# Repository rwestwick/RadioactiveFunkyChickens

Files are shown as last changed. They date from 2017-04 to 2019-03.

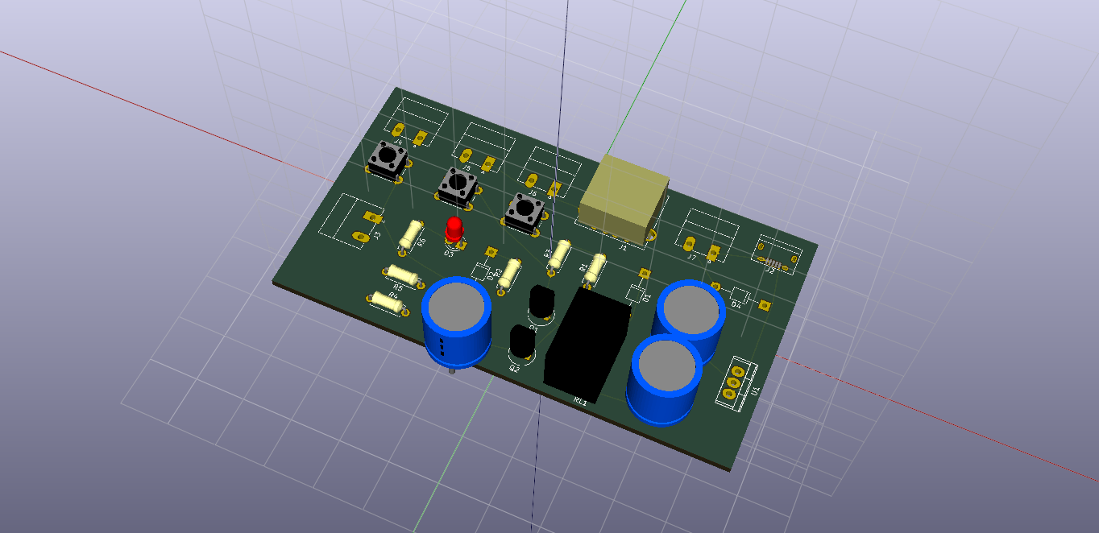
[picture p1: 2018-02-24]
Design/electronics/PiPowerSupplyCircuit/PowerSupplyAndSafeOff.png

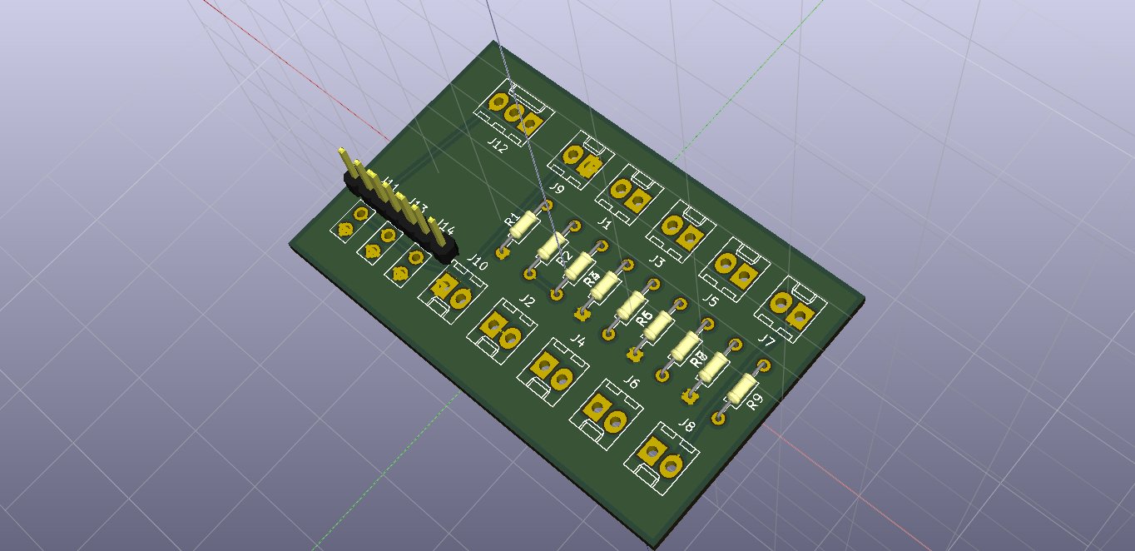
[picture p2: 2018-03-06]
Design/electronics/InterfaceBoard/InterfaceBoard.png

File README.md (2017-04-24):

# RadioactiveFunkyChickens

These are the Python files for the RadioactiveFunkyChickens team's PiWars robot.

## Files

### Challenge code

- LineFollowingAlgorithm.py: Code for the [line following challenge] (http://piwars.org/2017-competition/challenges/line-following/)
- MinimalMazeAlgorithm.py: Code for the [Minimal Maze challenge (http://piwars.org/2017-competition/challenges/minimal-maze/)
- straightLineSpeedTest2.py: Code for the [straight line speed test challenge] (http://piwars.org/2017-competition/challenges/straight-line-speed-test/)
- WiimoteControllerNunchukEye.py: Remote controller code to the non-autonomous PiWars challenges. Needs Wiimote Nunchuck and can control the servos for pan and tilt.

### Initio code

Several of the Python files are downloaded from the 4tronix web site to work with the Initio and Robohat hardware.

## See Also

- [RadioactiveFunkyChickens Blog] (https://radioactivefunkychickens.wordpress.com/)
- [PiWars] (http://piwars.org/)
- [Raspberry Pi] (http://www.raspberrypi.org/)
- [4tronix Initio Home Page] (http://4tronix.co.uk/blog/?p=169)

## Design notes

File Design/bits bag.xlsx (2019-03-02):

Hackaday perma proto black hat | £7.50 | https://thepihut.com/products/adafruit-perma-proto-hat-for-pi-mini-kit-with-eeprom
Raspberry Pi 3 Desktop Kit | £50.00 | https://thepihut.com/products/raspberry-pi-3-desktop-kit
Picon Zero - Intelligent Robotics Controller for Raspberry Pi | £16.00 | https://shop.pimoroni.com/products/picon-zero-intelligent-robotics-controller-for-raspberry-pi
RasPiO InsPiRing - Straight 8 + Driver | £10.00 | https://shop.rasp.io/collections/raspio-collection/products/raspio-inspiring-programmable-rgb-led-shapes-super-bright-and-colourful
PIR Motion Sensor Module | £2.00 | https://thepihut.com/products/pir-motion-sensor-module
Pi-DACZero (Pre Soldered) | £16.50 | http://iqaudio.co.uk/hats/38-pi-daczero.html
Raspberry Pi 3B+ with 16GB MicroSD | £40.00 | https://thepihut.com/collections/raspberry-pi-3b/products/raspberry-pi-3-model-b-plus
Weird Wiley bag x 2 | £0.00 | ??
Nostarch Book voucher (Code is good for one ebook up to $50) | £36.00 | www.nostarch.com | Code is good for one ebook up to $50
 | £178.00

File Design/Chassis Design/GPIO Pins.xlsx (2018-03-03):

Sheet: Current GPIO Pins - Robohat
 | Pin No.
 | 1 | 2
 | 3 | 4
 | 5 | 6
Not on Robohat | 7 | 8
 | 9 | 10
Not on Robohat | 11 | 12 | Sonar Left
Free Input on GPIO | 13 | 14
Sonar Left | 15 | 16 | Sonar Right
 | 17 | 18 | Servo
 | 19 | 20
 | 21 | 22 | Servo
 | 23 | 24
 | 25 | 26
 | 27 | 28
Not on Robohat | 29 | 30
Sonar Right | 31 | 32 | Right Motor
Right Motor | 33 | 34
Left Motor | 35 | 36 | Left Motor
Not on Robohat | 37 | 38 | Sonar Front
 | 39 | 40 | Not on Robohat

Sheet: GPIO Pins - L298N
 | Pin No.
 | 1 | 2
 | 3 | 4
 | 5 | 6
Left Motor - Rear | 7 | 8
 | 9 | 10
Left Motor - Rear | 11 | 12 | Sonar Left
Free | 13 | 14
Sonar Left | 15 | 16 | Sonar Right
 | 17 | 18 | Servo
 | 19 | 20
 | 21 | 22 | Servo
 | 23 | 24
 | 25 | 26
 | 27 | 28
Right Motor - Rear | 29 | 30
Sonar Right | 31 | 32 | Right Motor - Front
Right Motor - Front | 33 | 34
Left Motor - Front | 35 | 36 | Left Motor - Front
Right Motor - Rear | 37 | 38 | Sonar Front
 | 39 | 40 | Sonar Front
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

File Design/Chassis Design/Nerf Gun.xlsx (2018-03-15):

Theta | 30 | deg | One direction
Adjacent | 35 | mm
Opposite | 20.20725942 | mm
Travel for positive and negative angle
 | 40.41451884 | mm

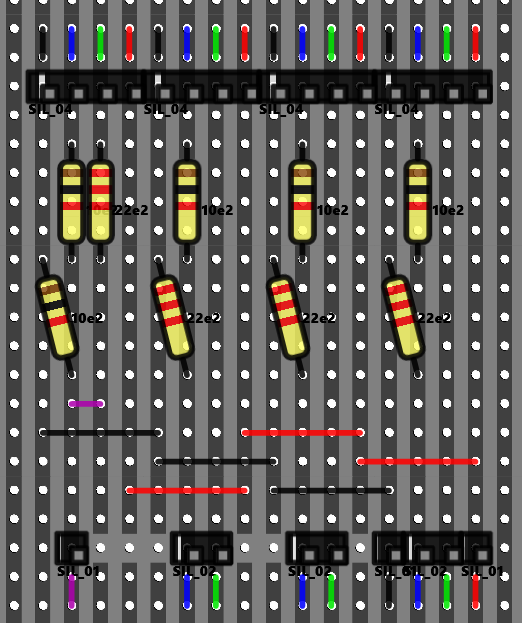
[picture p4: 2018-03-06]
Design/electronics/ultrasonic/ultrasonic.png

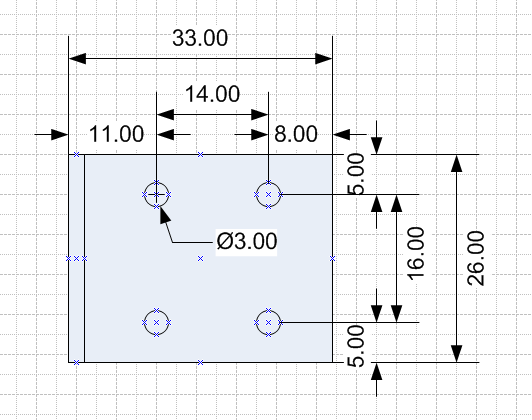
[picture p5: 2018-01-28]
Design/Chassis Design/6v_Motor_Bracket.png

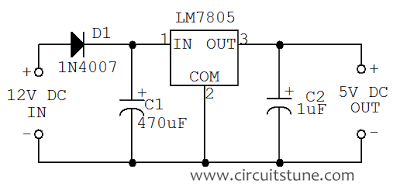
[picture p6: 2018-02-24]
Design/electronics/PiPowerSupplyCircuit/12-to-5-volt-dc-to-dc-converter-circuit-diagram.png

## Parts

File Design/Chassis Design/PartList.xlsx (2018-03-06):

Item | RS Code | Pack # | Per | Price (inc vat) | Total
Phoenix Contact COMBICON MPT Series 2.54mm Pitch Straight, PCB Terminal Block, Through Hole, 2 Way | 220-4260 | 5 | 5 | £0.49 | £2.47
Molex KK 254 6410, 2.54mm Pitch, 6 Way, 1 Row, Straight PCB Header, Through Hole | 483-8506 | 10 | 10 | £0.32 | £3.15
Bright Zinc Plated, Clear Passivated Steel Pan Head Machine Screws, M3 x 10mm | 560-596 | 100 | 1 | £2.81 | £2.81
Bright Zinc Plated, Clear Passivated Steel Pan Head Machine Screws, M3 x 12mm | 560-603 | 100 | 1 | £3.04 | £3.04
Molex KK 254 6471, 2.54mm Pitch, 6 Way, 1 Row Female Straight Connector Housing | 296-4984 | 5 | 5 | £0.54 | £2.70

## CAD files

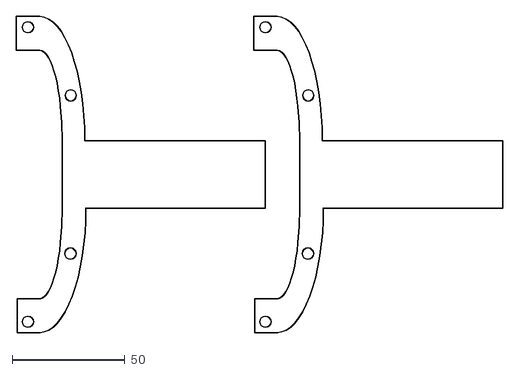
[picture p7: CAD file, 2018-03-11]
Design/Chassis Design/Slightly Deranged Golf - Layers.dxf
215.6 x 140.0

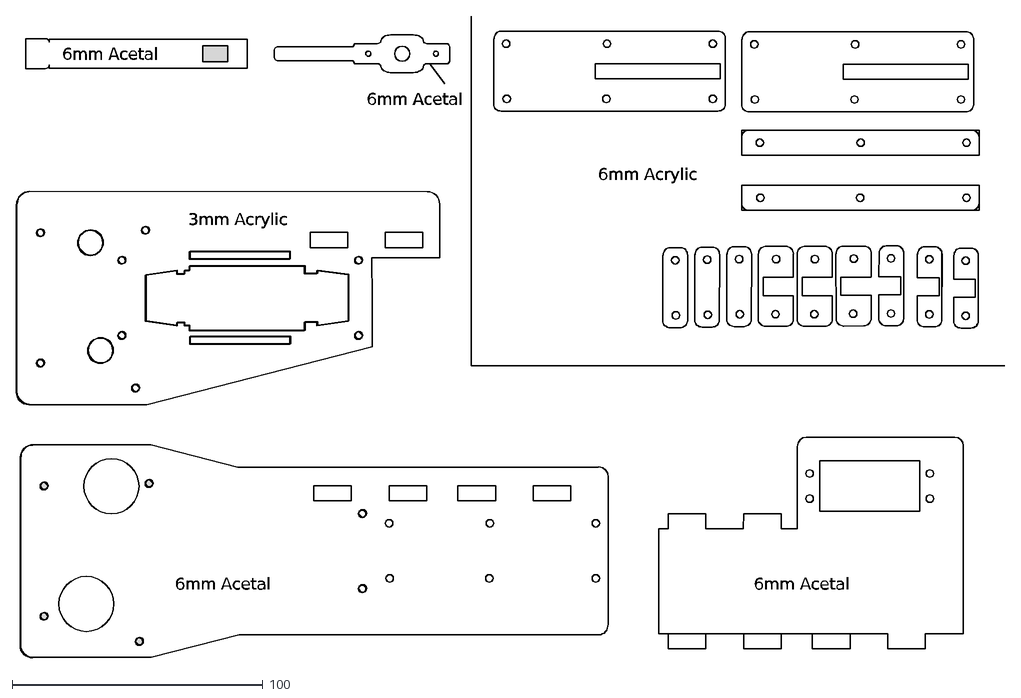
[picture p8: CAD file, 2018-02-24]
Design/Chassis Design/Nerf Holder.dxf
6mm Acetal
3mm Acrylic
6mm Acrylic

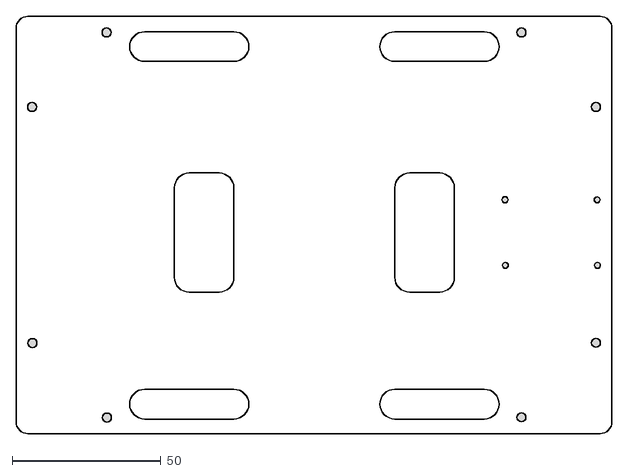
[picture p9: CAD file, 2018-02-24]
Design/Chassis Design/Pi Wars Chassis.dxf
200.0 x 140.0

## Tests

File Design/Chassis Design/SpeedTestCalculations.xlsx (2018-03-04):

Motor RPM | 270 | rpm
Wheel Dia | 65 | mm
Track Length | 7300 | mm
Rotation Lenth | 204.2 | mm
Num Rotations | 35.7 | #
Num Rotation per S | 4.5 | #
Est Time Taken | 7.94 | Seconds

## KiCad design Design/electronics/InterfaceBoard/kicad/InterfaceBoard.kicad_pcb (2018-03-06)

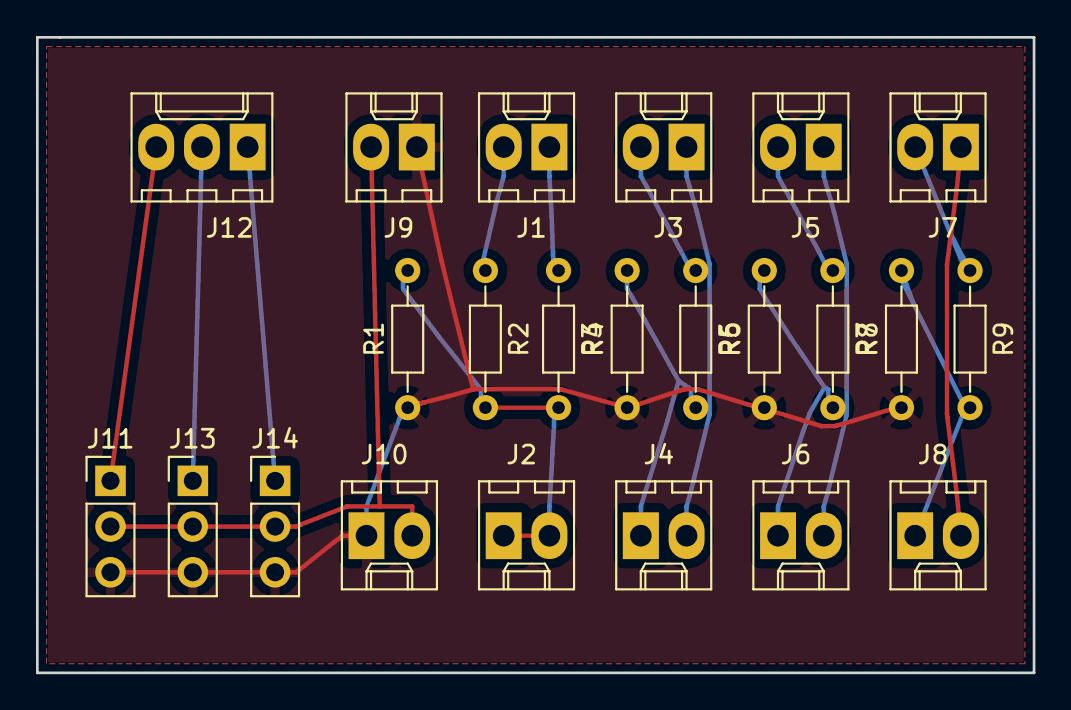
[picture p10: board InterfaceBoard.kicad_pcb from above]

Board: 2 copper layers, 55.4 x 35.3 mm, 23 parts (0 on the bottom side), 17 nets.

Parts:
J1, J2: PROX1; Molex_KK-6410-02_02x2.54mm_Straight
J3, J4: PROX2; Molex_KK-6410-02_02x2.54mm_Straight
J5, J6: PROX3; Molex_KK-6410-02_02x2.54mm_Straight
J7, J8: PROX4; Molex_KK-6410-02_02x2.54mm_Straight
J9: PWR IN; Molex_KK-6410-02_02x2.54mm_Straight
J10: PWR OUT; Molex_KK-6410-02_02x2.54mm_Straight
J11: HORZ; Pin_Header_Straight_1x03_Pitch2.54mm
J12: SERVO_IN; Molex_KK-6410-03_03x2.54mm_Straight
J13: VERT; Pin_Header_Straight_1x03_Pitch2.54mm
J14: FIRE; Pin_Header_Straight_1x03_Pitch2.54mm
R1, R2, R5, R7, R9: 1k; R_Axial_DIN0204_L3.6mm_D1.6mm_P7.62mm_Horizontal
R3, R4, R6, R8: 2k2; R_Axial_DIN0204_L3.6mm_D1.6mm_P7.62mm_Horizontal

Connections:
+5V: J9.2, J10.2, J11.2, J13.2, J14.2
GND: J9.1, J10.1, J11.3, J13.3, J14.3, R1.1, R4.1, R6.1, R8.1
unnamed: J1.1, R3.1
unnamed: J1.2, R2.1
unnamed: J2.1, J2.2, R1.2, R2.2, R3.2
unnamed: J3.1, J4.2
unnamed: J3.2, R5.1
unnamed: J4.1, R4.2, R5.2
unnamed: J5.1, J6.2
unnamed: J5.2, R7.1
unnamed: J6.1, R6.2, R7.2
unnamed: J7.1, J8.2
unnamed: J7.2, R9.1
unnamed: J8.1, R8.2, R9.2
unnamed: J11.1, J12.3
unnamed: J12.1, J14.1
unnamed: J12.2, J13.1

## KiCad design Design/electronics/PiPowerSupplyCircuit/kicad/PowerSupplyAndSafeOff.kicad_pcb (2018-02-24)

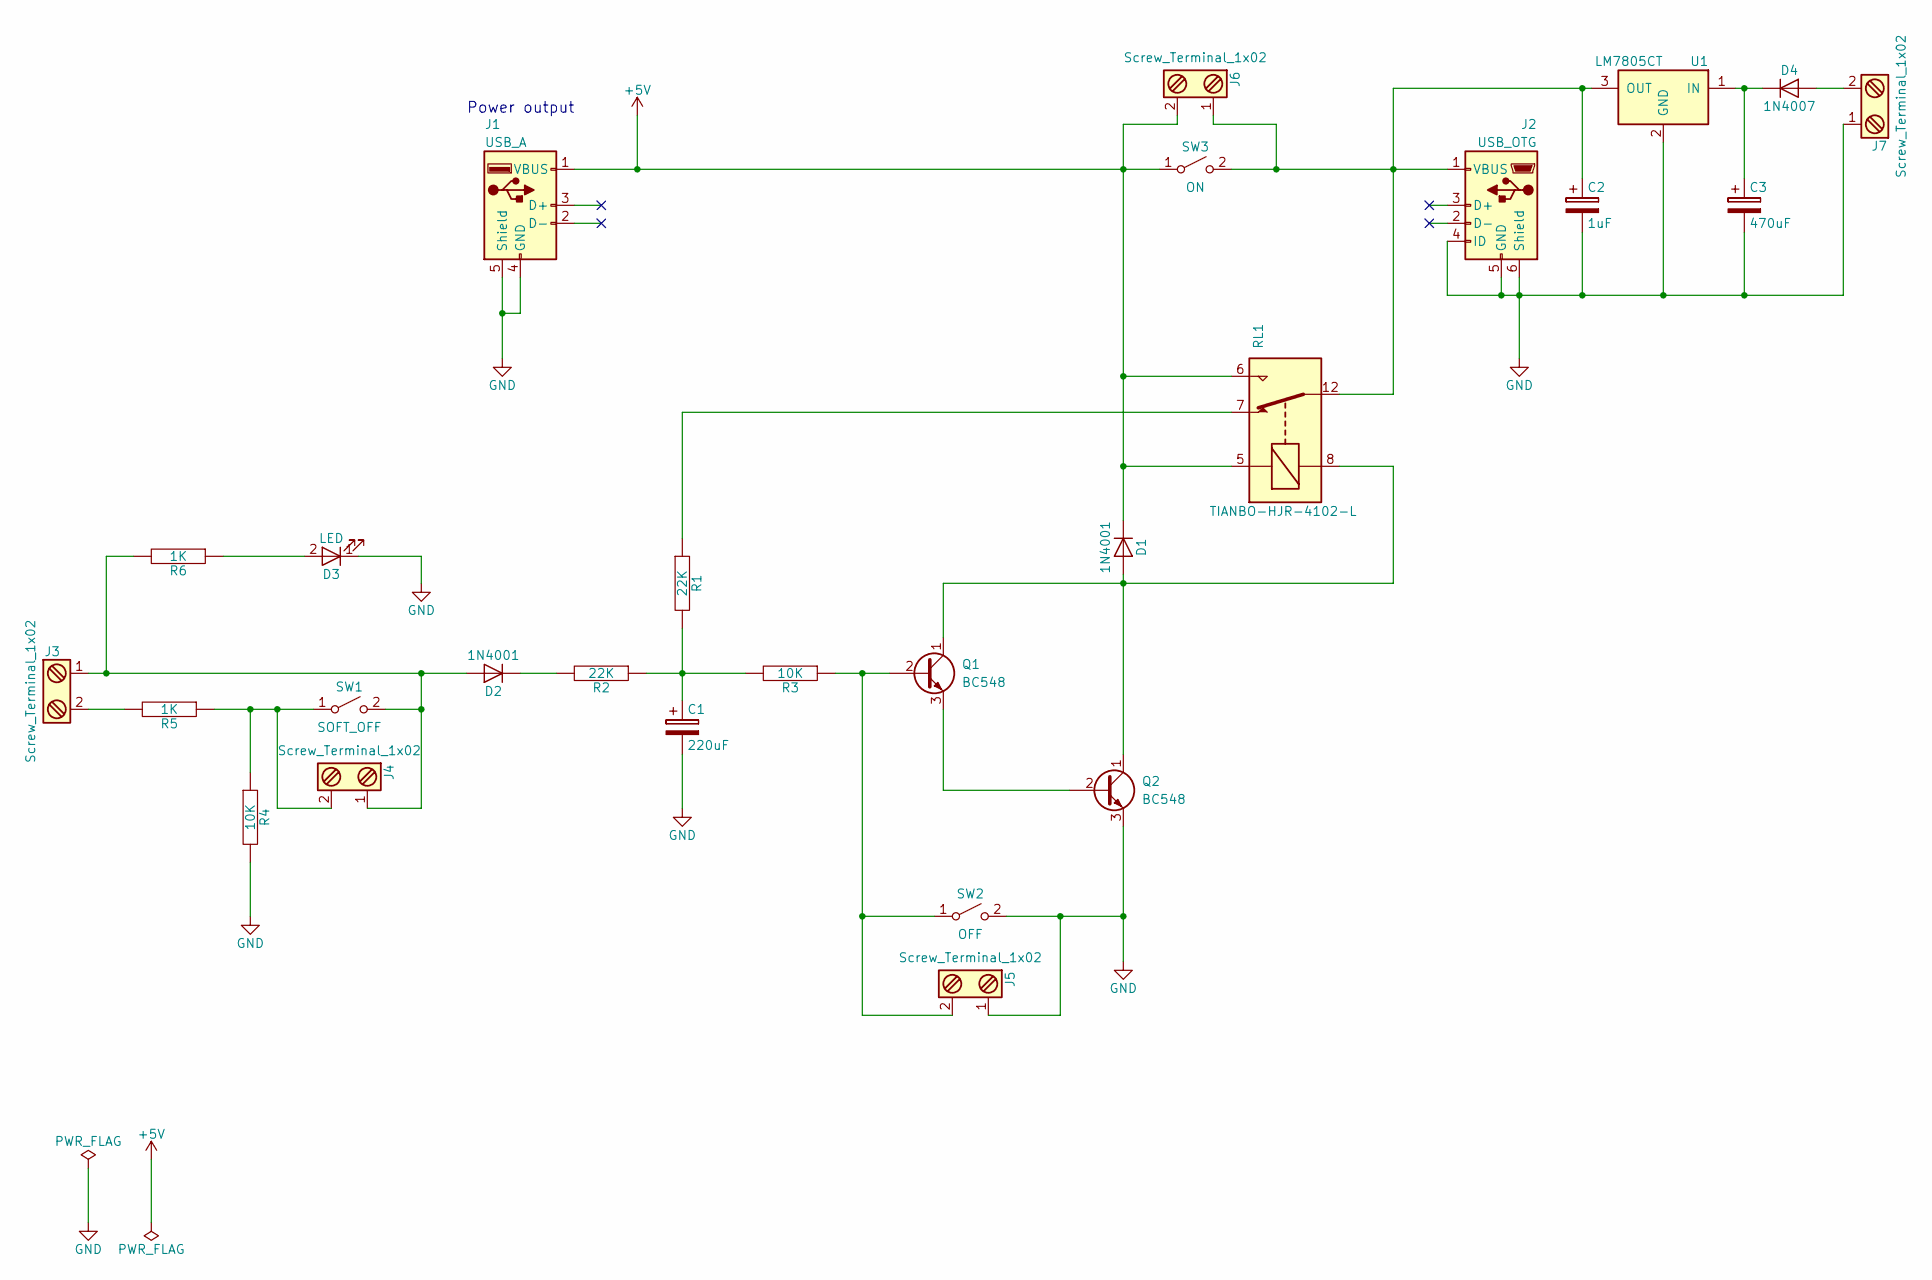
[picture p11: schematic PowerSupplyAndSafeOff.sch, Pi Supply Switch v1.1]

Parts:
C1: 220uF; CP_Radial_D5.0mm_P2.50mm
C2: 1uF; CP_Radial_D5.0mm_P2.50mm
C3: 470uF; CP_Radial_D5.0mm_P2.50mm
D1, D2: 1N4001; D_T-1_P10.16mm_Horizontal
D3: LED; LED_D3.0mm
D4: 1N4007; D_T-1_P10.16mm_Horizontal
J1: USB_A
J2: USB_OTG; USB_Micro-B
J3, J4, J5, J6, J7: Screw_Terminal_1x02; PhoenixContact_MC-G_02x5.08mm_Angled
Q1, Q2: BC548; TO-92_Inline_Narrow_Oval
R1, R2: 22K; R_Axial_DIN0207_L6.3mm_D2.5mm_P7.62mm_Horizontal
R3, R4: 10K; R_Axial_DIN0207_L6.3mm_D2.5mm_P7.62mm_Horizontal
R5, R6: 1K; R_Axial_DIN0207_L6.3mm_D2.5mm_P7.62mm_Horizontal
RL1: TIANBO-HJR-4102-L; Relay_SPDT_HJR-4102
SW1: SOFT_OFF; SW_PUSH_6mm_h4.3mm
SW2: OFF; SW_PUSH_6mm_h4.3mm
SW3: ON; SW_PUSH_6mm_h4.3mm
U1: LM7805CT; TO-220

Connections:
+5V: D1.1 (K), J1.1 (VBUS), J6.2, RL1.5, RL1.6, SW3.1 (A)
GND: C1.2, C2.2, C3.2, D3.1 (K), J1.4 (GND), J1.5 (Shield), J2.4 (ID), J2.5 (GND), J2.6 (Shield), J5.1, J7.1, Q2.3 (E), R4.2, SW2.2 (B), U1.2 (GND)
unnamed: C1.1, R1.2, R2.1, R3.2
unnamed: C2.1, J2.1 (VBUS), J6.1, RL1.12, SW3.2 (B), U1.3 (OUT)
unnamed: C3.1, D4.1 (K), U1.1 (IN)
unnamed: D1.2 (A), Q1.1 (C), Q2.1 (C), RL1.8
unnamed: D2.1 (K), R2.2
unnamed: D2.2 (A), J3.1, J4.1, R6.2, SW1.2 (B)
unnamed: D3.2 (A), R6.1
unnamed: D4.2 (A), J7.2
unnamed: J3.2, R5.2
unnamed: J4.2, R4.1, R5.1, SW1.1 (A)
unnamed: J5.2, Q1.2 (B), R3.1, SW2.1 (A)
unnamed: Q1.3 (E), Q2.2 (B)
unnamed: R1.1, RL1.7

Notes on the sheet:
Power output

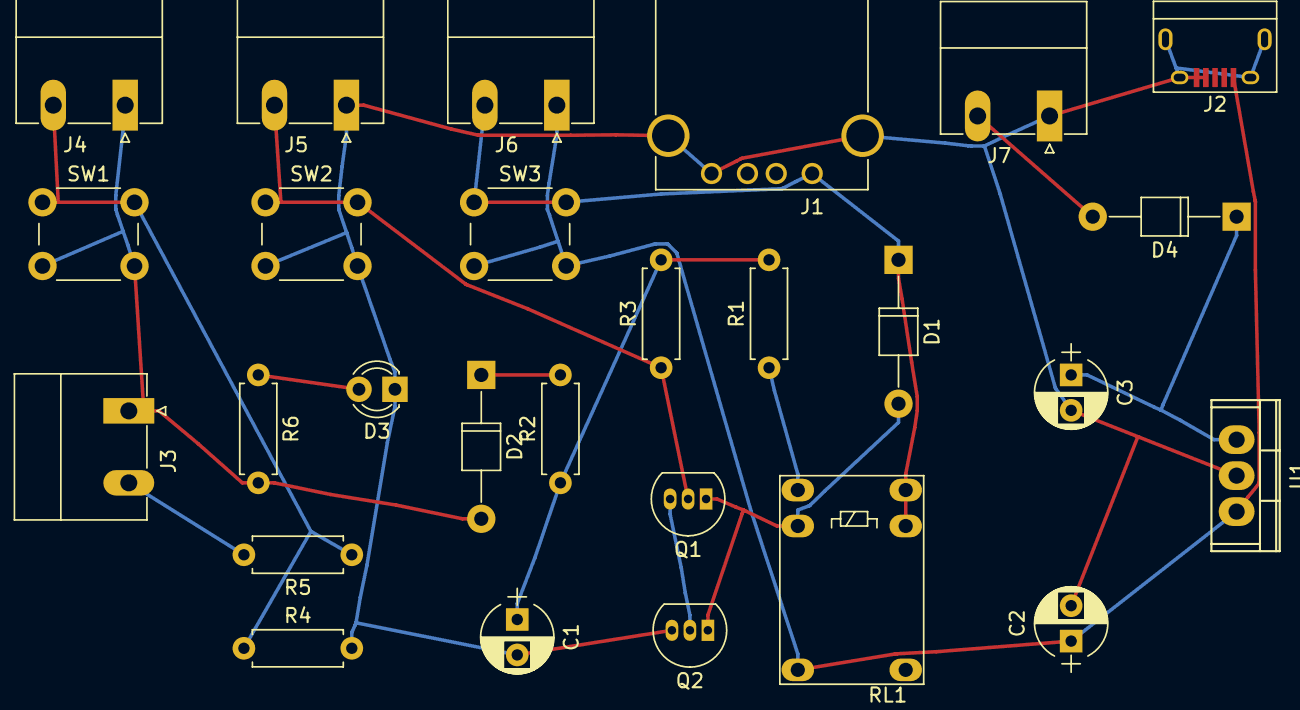
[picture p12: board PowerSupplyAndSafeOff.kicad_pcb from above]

Board: 2 copper layers, 27 parts (0 on the bottom side), 15 nets.

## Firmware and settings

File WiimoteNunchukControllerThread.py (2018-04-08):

#!/usr/bin/python
"""
Class defines how to interact with a Wiimote and Nunchuk
Controller via a thread

Need to install correct python modules, see
https://help.ubuntu.com/community/CWiiD
"""

import time
import logging
import threading
import math
import cwiid
import ServoController
import DualMotorController
import GPIOLayout
import SpeedSettings

MODULE_LOGGER = logging.getLogger("__main__.WiimoteNunchukControllerThread")


class WiimoteNunchukControllerThread(threading.Thread):
    """
    Defines the generic wiimote and nunchuk control mechanism
    """
    # Set constants
    STICK_DELAY = 0.1  # seconds
    BUTTON_DELAY = 0.25  # seconds
    PAN_STEP = 10
    TILT_STEP = 10
    NUNCHUK_MAX = 220.0
    NUNCHUK_MID = 126.0
    NUNCHUK_MIN = 32.0
    NUNCHUK_BUFFER = 25.0

    def __init__(self,
                 callback_b,
                 callback_c,
                 callback_z,
                 servo_controller=None):
        """
        Initialise the parameters required for WiimoteNunchukControllerThread
        """
        MODULE_LOGGER.info("Setting up WiimoteNunchukControllerThread Module")

        self._mutex = threading.Lock()
        self.t_val = 0  # 0 degrees is centre
        self.p_val = 0  # 0 degrees is centre

        self._exit_now = False
        self._servo_supplied = False
        self._button_b_callback = callback_b
        self._button_c_callback = callback_c
        self._button_z_callback = callback_z
        self.speed = SpeedSettings.SPEED_FASTEST  # Initial forward speed
        self.servo_controller = None

        # Initialise motors
        self.robotmove = DualMotorController.DualMotorController(
            GPIOLayout.MOTOR_LEFT_FRONT_FORWARD_GPIO,
            GPIOLayout.MOTOR_LEFT_FRONT_BACKWARD_GPIO,
            GPIOLayout.MOTOR_RIGHT_FRONT_FORWARD_GPIO,
            GPIOLayout.MOTOR_RIGHT_FRONT_BACKWARD_GPIO,
            GPIOLayout.MOTOR_LEFT_REAR_FORWARD_GPIO,
            GPIOLayout.MOTOR_LEFT_REAR_BACKWARD_GPIO,
            GPIOLayout.MOTOR_RIGHT_REAR_FORWARD_GPIO,
            GPIOLayout.MOTOR_RIGHT_REAR_BACKWARD_GPIO)

        # Initialise ServoController
        if servo_controller is not None:
            MODULE_LOGGER.debug("Using supplied servo controller")
            self.servo_controller = servo_controller
            self._servo_supplied = True
        else:
            MODULE_LOGGER.debug("Creating servo controller")
            self.servo_controller = ServoController.ServoController()
            self._servo_supplied = False

        self.servo_controller.start_servos()

        # Wiimote Controller
        self.wm = None

        threading.Thread.__init__(self)

    def __del__(self):
        """
        Destructor
        """
        if not self._exit_now:
            self.exit_now()

        if not self._servo_supplied and self.servo_controller is not None:
            self.servo_controller.stop_servos()

        self.robotmove.cleanup()
        MODULE_LOGGER.info("Wiimote Controller Finished")

    def __wiimote_connection(self):
        """
        Performs the loop within the thread
        """
        MODULE_LOGGER.info("Press 1+2 on your Wiimote now ...")

        i = 1
        while not self.wm and not self._exit_now:
            try:
                self.wm = cwiid.Wiimote()
            except RuntimeError:
                if (i > 5):
                    MODULE_LOGGER.error("Cannot create Wiimote connection.")
                    self.exit_now()
                MODULE_LOGGER.warning(
                    "Error opening wiimote connection, attempt " + str(i))
                i += 1

        if not self._exit_now:
            MODULE_LOGGER.info("Wiimote connected.")

            # Set wiimote to report button presses
            self.wm.rpt_mode = cwiid.RPT_BTN | cwiid.RPT_ACC | cwiid.RPT_EXT

            # Turn on led to show connected
            self.wm.led = 1

            # Add a delay to allow the wiimote to come up correctly
            time.sleep(1)

    def exit_now(self):
        """
        Request the thread to exit
        """
        MODULE_LOGGER.info("Request to exit")
        self._exit_now = True

    def run(self):
        """
        Performs the loop within the thread
        """
        self.__wiimote_connection()

        MODULE_LOGGER.debug("Starting loop thread")
        while not self._exit_now:
            if 'nunchuk' in self.wm.state:

                buttons = self.wm.state['buttons']
                nunchuck_buttons = self.wm.state['nunchuk']['buttons']

                # X axis: Left Max = 25, Middle = 124, Right Max = 225
                NunchukStickX = (self.wm.state['nunchuk']['stick'][cwiid.X])
                # Y axis: Down Max = 30, Middle = 132, Up Max = 225
                NunchukStickY = (self.wm.state['nunchuk']['stick'][cwiid.Y])

                # Go forward if joystick pushed forward beyond buffer in central
                # channel
                if (NunchukStickY > (self.NUNCHUK_MID + self.NUNCHUK_BUFFER)
                        and NunchukStickX <
                    (self.NUNCHUK_MID + self.NUNCHUK_BUFFER)
                        and NunchukStickX >
                        (self.NUNCHUK_MID - self.NUNCHUK_BUFFER)):

                    self.speed = int(SpeedSettings.SPEED_FASTEST *
                                     (NunchukStickY - self.NUNCHUK_MID) /
                                     (self.NUNCHUK_MAX - self.NUNCHUK_MID))
                    if self.speed > SpeedSettings.SPEED_FASTEST:
                        self.speed = SpeedSettings.SPEED_FASTEST

                    MODULE_LOGGER.debug("Forward at speed " + str(self.speed))
                    self.robotmove.forward(self.speed)
                    time.sleep(self.STICK_DELAY)

                # Go backwards if joystick pulled back beyond buffer in central
                # channel
                elif (NunchukStickY < (self.NUNCHUK_MID - self.NUNCHUK_BUFFER)
                      and NunchukStickX <
                      (self.NUNCHUK_MID + self.NUNCHUK_BUFFER)
                      and NunchukStickX >
                      (self.NUNCHUK_MID - self.NUNCHUK_BUFFER)):

                    self.speed = int(SpeedSettings.SPEED_FASTEST *
                                     (self.NUNCHUK_MID - NunchukStickY) /
                                     (self.NUNCHUK_MID - self.NUNCHUK_MIN))
                    if self.speed > SpeedSettings.SPEED_FASTEST:
                        self.speed = SpeedSettings.SPEED_FASTEST

                    MODULE_LOGGER.debug("Reverse at speed " + str(self.speed))
                    self.robotmove.reverse(self.speed)
                    time.sleep(self.STICK_DELAY)

                # Spin right right joystick pushed right beyond buffer in central
                # channel
                elif (NunchukStickX > (self.NUNCHUK_MID + self.NUNCHUK_BUFFER)
                      and NunchukStickY <
                      (self.NUNCHUK_MID + self.NUNCHUK_BUFFER)
                      and NunchukStickY >
                      (self.NUNCHUK_MID - self.NUNCHUK_BUFFER)):

                    self.speed = int(SpeedSettings.SPEED_FASTEST *
                                     (NunchukStickX - self.NUNCHUK_MID) /
                                     (self.NUNCHUK_MAX - self.NUNCHUK_MID))
                    if self.speed > SpeedSettings.SPEED_FASTEST:
                        self.speed = SpeedSettings.SPEED_FASTEST

                    MODULE_LOGGER.debug(
                        "Spin right at speed " + str(self.speed))
                    self.robotmove.spin_right(self.speed)
                    time.sleep(self.STICK_DELAY)

                # Spin left if joystick pushed left beyond buffer in central
                # channel
                elif (NunchukStickX < (self.NUNCHUK_MID - self.NUNCHUK_BUFFER)
                      and NunchukStickY <
                      (self.NUNCHUK_MID + self.NUNCHUK_BUFFER)
                      and NunchukStickY >
                      (self.NUNCHUK_MID - self.NUNCHUK_BUFFER)):

                    self.speed = int(SpeedSettings.SPEED_FASTEST *
                                     (self.NUNCHUK_MID - NunchukStickX) /
                                     (self.NUNCHUK_MID - self.NUNCHUK_MIN))
                    if self.speed > SpeedSettings.SPEED_FASTEST:
                        self.speed = SpeedSettings.SPEED_FASTEST

                    MODULE_LOGGER.debug(
                        "Spin left at speed " + str(self.speed))
                    self.robotmove.spin_left(self.speed)
                    time.sleep(self.STICK_DELAY)

                # Turn forward left if joystick pushed top left outside central
                # channels
                elif (NunchukStickX < (self.NUNCHUK_MID - self.NUNCHUK_BUFFER)
                      and NunchukStickY >
                      (self.NUNCHUK_MID + self.NUNCHUK_BUFFER)):

                    # Calculate lengths in range <100, min value depends on
                    # self.NUNCHUK_BUFFER value
                    lengthX = SpeedSettings.SPEED_FASTEST * \
                        (self.NUNCHUK_MID - NunchukStickX) / \
                        (self.NUNCHUK_MID - self.NUNCHUK_MIN)
                    lengthY = SpeedSettings.SPEED_FASTEST * \
                        (NunchukStickY - self.NUNCHUK_MID) / \
                        (self.NUNCHUK_MAX - self.NUNCHUK_MID)

                    # self.speed is length of hypotenuse from Pythagoras
                    overall_speed = int(
                        math.sqrt(math.pow(lengthX, 2) + math.pow(lengthY, 2)))

                    if overall_speed > SpeedSettings.SPEED_FASTEST:
                        overall_speed = SpeedSettings.SPEED_FASTEST
                    if lengthY > SpeedSettings.SPEED_FASTEST:
                        lengthY = SpeedSettings.SPEED_FASTEST

                    # Calculate wheel self.speeds
                    self.speedLeftWheel = int(lengthY)
                    self.speedRightWheel = overall_speed

                    MODULE_LOGGER.debug(
                        "Steer left. Left wheel at speed: " +
                        str(self.speedLeftWheel) + " Right wheel at speed: " +
                        str(self.speedRightWheel))
                    self.robotmove.turn_forward(self.speedLeftWheel,
                                                self.speedRightWheel)
                    time.sleep(self.STICK_DELAY)

                # Turn forward right if joystick pushed top right outside central
                # channels
                elif (NunchukStickX > (self.NUNCHUK_MID + self.NUNCHUK_BUFFER)
                      and NunchukStickY >
                      (self.NUNCHUK_MID + self.NUNCHUK_BUFFER)):

                    # Calculate lengths in range <100, min value depends on
                    # self.NUNCHUK_BUFFER value
                    lengthX = SpeedSettings.SPEED_FASTEST * \
                        (self.NUNCHUK_MID - NunchukStickX) / \
                        (self.NUNCHUK_MID - self.NUNCHUK_MIN)
                    lengthY = SpeedSettings.SPEED_FASTEST * \
                        (NunchukStickY - self.NUNCHUK_MID) / \
                        (self.NUNCHUK_MAX - self.NUNCHUK_MID)

                    # self.speed is length of hypotenuse from Pythagoras
                    overall_speed = int(
                        math.sqrt(math.pow(lengthX, 2) + math.pow(lengthY, 2)))

                    if overall_speed > SpeedSettings.SPEED_FASTEST:
                        overall_speed = SpeedSettings.SPEED_FASTEST
                    if lengthY > SpeedSettings.SPEED_FASTEST:
                        lengthY = SpeedSettings.SPEED_FASTEST

                    # Calculate wheel self.speeds
                    self.speedLeftWheel = overall_speed
                    self.speedRightWheel = int(lengthY)

                    MODULE_LOGGER.debug(
                        "Steer right. Left wheel at speed: " +
                        str(self.speedLeftWheel) + " Right wheel at speed: " +
                        str(self.speedRightWheel))
                    self.robotmove.turn_forward(self.speedLeftWheel,
                                                self.speedRightWheel)
                    time.sleep(self.STICK_DELAY)

                # Turn reverse left if joystick pushed bottom left outside central
                # channels
                elif (NunchukStickX < (self.NUNCHUK_MID - self.NUNCHUK_BUFFER)
                      and NunchukStickY <
                      (self.NUNCHUK_MID - self.NUNCHUK_BUFFER)):

                    # Calculate lengths in range <100, min value depends on
                    # self.NUNCHUK_BUFFER value
                    lengthX = SpeedSettings.SPEED_FASTEST * \
                        (self.NUNCHUK_MID - NunchukStickX) / \
                        (self.NUNCHUK_MID - self.NUNCHUK_MIN)
                    lengthY = SpeedSettings.SPEED_FASTEST * \
                        (self.NUNCHUK_MID - NunchukStickY) / \
                        (self.NUNCHUK_MID - self.NUNCHUK_MIN)

                    # self.speed is length of hypotenuse from Pythagoras
                    overall_speed = int(
                        math.sqrt(math.pow(lengthX, 2) + math.pow(lengthY, 2)))

                    if overall_speed > SpeedSettings.SPEED_FASTEST:
                        overall_speed = SpeedSettings.SPEED_FASTEST
                    if lengthY > SpeedSettings.SPEED_FASTEST:
                        lengthY = SpeedSettings.SPEED_FASTEST

                    # Calculate wheel self.speeds
                    self.speedLeftWheel = int(lengthY)
                    self.speedRightWheel = overall_speed

                    MODULE_LOGGER.debug(
                        "Reverse left. Left wheel at speed: " +
                        str(self.speedLeftWheel) + " Right wheel at speed: " +
                        str(self.speedRightWheel))
                    self.robotmove.turn_reverse(self.speedLeftWheel,
                                                self.speedRightWheel)
                    time.sleep(self.STICK_DELAY)

                # Turn reverse right if joystick pushed top right outside central
                # channels
                elif (NunchukStickX > (self.NUNCHUK_MID + self.NUNCHUK_BUFFER)
                      and NunchukStickY <
                      (self.NUNCHUK_MID + self.NUNCHUK_BUFFER)):

                    # Calculate lengths in range <100, min value depends on
                    # self.NUNCHUK_BUFFER value
                    lengthX = SpeedSettings.SPEED_FASTEST * \
                        (self.NUNCHUK_MID - NunchukStickX) / \
                        (self.NUNCHUK_MID - self.NUNCHUK_MIN)
                    lengthY = SpeedSettings.SPEED_FASTEST * \
                        (self.NUNCHUK_MID - NunchukStickY) / \
                        (self.NUNCHUK_MID - self.NUNCHUK_MIN)

                    # self.speed is length of hypotenuse from Pythagoras
                    overall_speed = int(
                        math.sqrt(math.pow(lengthX, 2) + math.pow(lengthY, 2)))

                    if overall_speed > SpeedSettings.SPEED_FASTEST:
                        overall_speed = SpeedSettings.SPEED_FASTEST
                    if lengthY > SpeedSettings.SPEED_FASTEST:
                        lengthY = SpeedSettings.SPEED_FASTEST

                    # Calculate wheel self.speeds
                    self.speedLeftWheel = overall_speed
                    self.speedRightWheel = int(lengthY)

                    MODULE_LOGGER.debug(
                        "Reverse right. Left wheel at speed: " +
                        str(self.speedLeftWheel) + " Right wheel at speed: " +
                        str(self.speedRightWheel))
                    self.robotmove.turn_reverse(self.speedLeftWheel,
                                                self.speedRightWheel)
                    time.sleep(self.STICK_DELAY)

                # else stop
                else:
                    self.robotmove.stop()

                    # If button up pressed move servo up
                if (buttons & cwiid.BTN_UP):
                    self.t_val = self.t_val + self.TILT_STEP
                    if self.t_val > 90:
                        self.t_val = 90
                    self.servo_controller.set_tilt_servo(self.t_val)
                    time.sleep(self.BUTTON_DELAY)

                # If button down pressed move servo down
                elif (buttons & cwiid.BTN_DOWN):
                    self.t_val = self.t_val - self.TILT_STEP
                    if self.t_val < -90:
                        self.t_val = -90
                    self.servo_controller.set_tilt_servo(self.t_val)
                    time.sleep(self.BUTTON_DELAY)

                # If button right pressed move servo right
                elif (buttons & cwiid.BTN_RIGHT):
                    self.p_val = self.p_val + self.PAN_STEP
                    if self.p_val > 90:
                        self.p_val = 90
                    self.servo_controller.set_pan_servo(self.p_val)
                    time.sleep(self.BUTTON_DELAY)

                # If button left pressed move servo left
                elif (buttons & cwiid.BTN_LEFT):
                    self.p_val = self.p_val - self.PAN_STEP
                    if self.p_val < -90:
                        self.p_val = -90
                    self.servo_controller.set_pan_servo(self.p_val)
                    time.sleep(self.BUTTON_DELAY)

                # If button A pressed centre Servo
                elif (buttons & cwiid.BTN_A):
                    self.p_val = 0
                    self.t_val = 0
                    self.servo_controller.set_pan_servo(self.p_val)
                    self.servo_controller.set_tilt_servo(self.t_val)
                    MODULE_LOGGER.debug("Centre!")
                    time.sleep(self.BUTTON_DELAY)

                # If button B pressed rumble Wiimote, but don't block other
                # actions
                if (buttons & cwiid.BTN_B):
                    if self._button_b_callback is not None:
                        self._button_b_callback(self.wm)
                        time.sleep(self.BUTTON_DELAY)

                # If button C pressed Toggle the targeting laser
                if (nunchuck_buttons & cwiid.NUNCHUK_BTN_C):
                    if self._button_c_callback is not None:
                        self._button_c_callback(self.wm)
                        time.sleep(self.BUTTON_DELAY)

                # If button z pressed Toggle the nerf gun fly wheels
                if (nunchuck_buttons & cwiid.NUNCHUK_BTN_Z):
                    if self._button_z_callback is not None:
                        self._button_z_callback(self.wm)
                        time.sleep(self.BUTTON_DELAY)

        MODULE_LOGGER.debug("Finished thread")

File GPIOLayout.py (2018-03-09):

# !/usr/bin/python
"""
Defines the various 2018 robot GPIO pins
"""

# Motor Pins two controllers
MOTOR_LEFT_FRONT_FORWARD_GPIO = 5  # Pin 29
MOTOR_LEFT_FRONT_BACKWARD_GPIO = 26  # Pin 37
MOTOR_LEFT_REAR_FORWARD_GPIO = 19  # Pin 35
MOTOR_LEFT_REAR_BACKWARD_GPIO = 12  # Pin 32
MOTOR_RIGHT_FRONT_FORWARD_GPIO = 4  # Pin 7
MOTOR_RIGHT_FRONT_BACKWARD_GPIO = 17  # Pin 11
MOTOR_RIGHT_REAR_FORWARD_GPIO = 13  # Pin 33
MOTOR_RIGHT_REAR_BACKWARD_GPIO = 16  # Pin 36

# Duck Shoot
DUCK_SHOOT_FIRE_PIN = 13  # GPIO27
DUCK_SHOOT_LASER_GPIO = 14  # Pin 8
DUCK_SHOOT_MOTOR_GPIO = 21  # Pin 40

# Define Sonar Pins
SONAR_FRONT_TX_GPIO = 20  # Pin 38
SONAR_FRONT_RX_GPIO = 20  # Pin 38
SONAR_LEFT_TX_GPIO = 18  # Pin 12
SONAR_LEFT_RX_GPIO = 22  # Pin 15
SONAR_RIGHT_TX_GPIO = 6  # Pin 31
SONAR_RIGHT_RX_GPIO = 23  # Pin 16

# Line follower
# Pins used for dual motor controllers
LINE_FOLLOWER_LEFT_GPIO = 4  # Pin 7
LINE_FOLLOWER_MIDDLE_GPIO = 17  # Pin 11
LINE_FOLLOWER_RIGHT_GPIO = 5  # Pin 29

# Servo Pins
SERVO_PAN_PIN = 22  # GPIO25
SERVO_TILT_PIN = 18  # GPIO24

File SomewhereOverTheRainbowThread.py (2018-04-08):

#!/usr/bin/env python
# -*- coding: utf-8 -*-
#
#  SomewhereOverTheRainbowThread.py
# http://piwars.org/2018-competition/challenges/somewhere-over-the-rainbow/
"""
This algorithm is designed to solve the Somewhere Over the Rainbow Pi Wars 4.0
challenge.
"""

# https://www.python.org/dev/peps/pep-0238/
# The future division statement, spelled "from __future__ import division",
# will change the / operator to mean true division throughout the module.
# This is needed for the row and column calculations for rectangle arrays to
# prevent rounding down to zero.
from __future__ import division
import logging
import time
import math
import cv2
import numpy as np
import SetupConsoleLogger
import ColourBoundaries
import GPIOLayout
import SpeedSettings
import ServoController
import DualMotorController
import UltrasonicSensorThread
import CameraThread

# Global values and their initial values
global debug  # Used for processing time
global debug_show_input  # Used to show input image
global debug_show_output  # Used to show image output after processing
global debug_show_steering  # Used to show steering outputs
global debug_show_tilt  # Used to show stilt value

# Create a logger to both file and stdout
LOGGER = logging.getLogger(__name__)
SetupConsoleLogger.setup_console_logger(LOGGER, logging.DEBUG)

debug = True
debug_show_input = True
debug_show_output = True
debug_show_steering = True
debug_show_tilt = True


# Image stream processing thread
# For threading tutourials see
# https://www.tutorialspoint.com/python/python_multithreading.htm
# http://www.bogotobogo.com/python/Multithread/python_multithreading_Event_Objects_between_Threads.php
class Processor(object):
    """
    """

    PAN_INTIAL = 0  # Initial pan angle in degrees
    TILT_INTIAL = 20  # Initial tilt angle in degrees
    TILT_CHANGE = 2  # Change in tilt angle in degrees to keep marker centred
    MIN_TILT = -40  # Minimum tilt angle in degrees
    MAX_TILT = 40  # Maximum tilt angle in degrees
    STEERING_RATE = 4.0  # Changes the speed at which it turns towards ball
    MAX_SPEED = SpeedSettings.SPEED_FAST
    MIN_SPEED = 0
    # Set movement constant values
    FRONT_BUFFER_WARN = 35  # Distance to corner for when to slow (cm)
    FRONT_BUFFER_STOP = 20  # Shortest distance to corner (cm)
    CENTRE_BUFFER_WARN = 65  # Distance from corner for when to slow (cm)
    CENTRE_BUFFER_STOP = 80  # Shortest distance from corner (cm)
    # ~86.2 cm from corner if perfect centre
    SPIN_TIME = 1.0  # Spin time in seconds
    # Image filtering constants
    # Aperture size for median filter based on PiBorg numbers of 5 with 320 *
    # 240
    MED_FILTER_APRTRE_SIZE = 5  # Must be odd number
    # Initial number for down selecting large contours
    # If number too small then will loose circular marker
    NUM_OF_LARGEST_AREA_CONTOURS = 3
    MIN_MARKER_AREA = 100  # Pixels - the final value to be decided from testing

    def __init__(self):
        """
        Constructor
        """
        LOGGER.debug("StreamProcessor constructor called")

        self.width = 320
        self.height = 240
        self.reached_marker = False
        self.servo_controller = ServoController.ServoController()
        self.servo_controller.start_servos()
        self.pan_angle = self.PAN_INTIAL
        self.tilt_angle = self.TILT_INTIAL
        self.servo_controller.set_pan_servo(self.pan_angle)
        self.servo_controller.set_tilt_servo(self.tilt_angle)
        time.sleep(1)
        self.colour_array_cntr = 0
        LOGGER.info("The colour selector starts as " +
                    ColourBoundaries.COLOUR_NAME_ARRAY[self.colour_array_cntr])

        # Initialise Ultrasonic Sensors
        self.FRONT_SENSOR = UltrasonicSensorThread.UltrasonicSensorThread(
            1, None, GPIOLayout.SONAR_FRONT_TX_GPIO,
            GPIOLayout.SONAR_FRONT_RX_GPIO, 1)
        self.FRONT_SENSOR.start()

        self.ROBOTMOVE = DualMotorController.DualMotorController(
            GPIOLayout.MOTOR_LEFT_FRONT_FORWARD_GPIO,
            GPIOLayout.MOTOR_LEFT_FRONT_BACKWARD_GPIO,
            GPIOLayout.MOTOR_RIGHT_FRONT_FORWARD_GPIO,
            GPIOLayout.MOTOR_RIGHT_FRONT_BACKWARD_GPIO,
            GPIOLayout.MOTOR_LEFT_REAR_FORWARD_GPIO,
            GPIOLayout.MOTOR_LEFT_REAR_BACKWARD_GPIO,
            GPIOLayout.MOTOR_RIGHT_REAR_FORWARD_GPIO,
            GPIOLayout.MOTOR_RIGHT_REAR_BACKWARD_GPIO)

    def __del__(self):
        """
        Destructor
        """
        self.cleanup()

    def cleanup(self):
        LOGGER.debug("starting cleanup")
        self.ROBOTMOVE.stop()
        self.ROBOTMOVE.cleanup()
        self.FRONT_SENSOR.exit_now()
        self.FRONT_SENSOR.join()
        self.servo_controller.stop_servos()

    def image_process_entry(self, bgr_image, width, height):
        """
        The main image processing function
        """
        global debug
        global debug_show_input
        global debug_show_output
        self.width = width
        self.height = height

        key_one = cv2.waitKey(1) & 0xFF

        # Find chosen colour in image
        colour_filtered_output, colour_filtered_mask = self.find_HSV_colour(
            bgr_image)

        # Find location of contour
        contour_detection, found_x, found_y, contour_marked_image = 
            self.find_marker_contour(
                colour_filtered_mask, colour_filtered_output)

        if debug_show_output:
            cv2.imshow('Filtered image with marker contour',
                       contour_marked_image)

            # Capture a key press. The function waits argument in ms
            # for any keyboard event
            # For some reason image does not show without this!
            key_two = cv2.waitKey(1) & 0xFF

        if key_one == ord("c") or key_two == ord("c"):
            # Loop over integers 0 to 3
            self.colour_array_cntr = (self.colour_array_cntr + 1) % 4
            LOGGER.info("The colour selector is now " + ColourBoundaries.
                        COLOUR_NAME_ARRAY[self.colour_array_cntr])

        if contour_detection:
            # Adjust tilt of Pi Camera
            self.set_camera_tilt_from_marker(found_y)

            # Steer robot
            distance_to_front_wall = self.FRONT_SENSOR.read_data()
            if not self.reached_marker:
                self.set_speed_from_marker(contour_detection, found_x,
                                           distance_to_front_wall)
            else:
                self.set_speed_to_centre(contour_detection, found_x,
                                         distance_to_front_wall)
        else:
            LOGGER.info("Spin right to find " + ColourBoundaries.
                        COLOUR_NAME_ARRAY[self.colour_array_cntr] + " marker.")
            self.spin_to_find_colour()
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

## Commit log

2016-11-06 Add files via upload
    Added simple file to do the proximity alert challenge. Motors not enabled by default so I can test code on my desk.
2017-02-07 Fixed issues with code following being able to actually run it!
    [UltrasonicSensor.py]
2017-02-07 Fixed issues with the ServoController
    [ServoController.py]
2017-02-07 Fixed issues with the MotorController
    [MotorController.py]
2017-02-07 Added a one wheel turn (left and right) to the MotorController
2017-02-07 Controller and Sensor code is now flake8 compliant
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2017-02-08 Made code pep8 compliant using flake8 IRSensor.py LineFollowerSensor.py MotorController.py ServoController.py UltrasonicSensor.py and pylint -f colorized -r no IRSensor.py LineFollowerSensor.py Motor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
2017-02-15 Added speed definitions to the motor controller Added a line following algorithm and modified to use the MotorController and LineFollowerSensor
2017-02-18 Added pylint config file and updated jenkins script to use it
    [pylint.cfg]
2017-02-19 Modified straight line speed test to use the new sensor and controller modules
2017-02-19 Tidyup logging in sensors and controllers. Complete moving the straight line speed test over ot the new libraries
2017-02-19 Added pin ids file and modified sensors controllers to take pin ids on initialisation
2017-02-19 initialised the motor controller with the pins from the new python file
2017-02-19 fixed old sonarrfc reference in straight line speed test
2017-02-19 updated speed to use the motor contorller defines
2017-02-19 Moved test files into test folder and tidied up sensor, controller and challenge code
2017-02-19 fixed pep8 issue and moved additional file to test folder
    [GPIOLayout.py, funkyChicken.py]
2017-02-19 More pep8 changes. Now ignoring issues in the test folder
    [SetupConsoleLogger.py]
2017-02-19 Fixed failure in the line follower
    [GPIOLayout.py, LineFollowingAlgorithm.py]
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2017-02-25 bug fixing on straight line speed test
    [MotorController.py]
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2017-02-26 Allow copy of servod to run robohat.py init() to run with no warnings.
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2017-02-28 Changing speed variable automatically applied to current direction.
2017-03-04 Added program to start testing line detection using RaspberryPi camera.
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2017-03-08 Generating error on buffer length.
    [LineFollowerCamera.py]
2017-03-11 Updated algorithm and removed small bug.
    [LineFollowerCameraAlg.py]
2017-03-11 Removed small test code as no longer needed.
    [LineFollowerCameraAlg.py]
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2017-03-11 fixed the line sensing and following algorithm to match the 4 wheel drive robot
    [LineFollowingAlgorithm.py, MotorController.py]
2017-03-15 Added comment to help install correct modules.
    [WiimoteController.py]
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2017-03-20 Turning check and small updates to the minimal maze algo
    [turning.xlsx]
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2017-11-11 Added ability to switch a gpio port on and off
2017-11-11 Full test of pan/tilt servo control in Python only.
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2017-11-12 Added & at end of a command and fixed some bugs.
    [ServoController.py]
2017-11-12 Corrected so that all p1 and added echo to command line.
    [ServoController.py]
2017-11-12 Fixed bugs, but pan angle still not zeroed correctly.
    [ServoController.py]
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2017-11-25 Fixed bug on largest contour, but still errors.
    [openCVcolorDetectLeftAndRight.py]
2017-11-26 Added Dual Motor driver controller Fixed gpio to match the correct wheels Updated dual motor tester programme
    [DualMotorController.py, GPIOLayout.py, MotorController.py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]
2017-11-26 Fixed the test programme to use the dual controller driver These motors are much better than before so gave better range of speeds
    [DualMotorController.py, TestDriverTwoControllersAlgorithm.py]
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2017-12-02 Added a new Mecanum controller which allows the movement afforded by the Mecanum wheel and dual motor controllers. Added a speed setting file as these were being duplicated in a number of places.
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2017-12-09 Added code for no contours detected reporting, but still needs correcting actions if that occurs.
    [SomewhereOverTheRainbow.py]
2017-12-10 Added code to handle no contours without functions not working and program stopping.
    [SomewhereOverTheRainbow.py]
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2017-12-17 fixed issues with the various levels of motorcontrollers. also noticed the gpio pins not set correctly. added another motor test function
    [DualMotorController.py, GPIOLayout.py, MecanumController.py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]
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2017-12-22 Updating code to filter out noise.
    [SomewhereOverTheRainbow.py]
2017-12-24 Broke down main() into separate functions.
    [SomewhereOverTheRainbow.py]
2017-12-24 Fixed bugon speed versus distance logic.
    [SomewhereOverTheRainbow.py]
2017-12-24 Fixed some pep8 and pylint
    [TestDriverTwoControllersAlgorithm.py]
2017-12-24 more automatic pep8 and pylint fixes
    [irTest.py, lineDetection.py, minimalMaze.py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]
2017-12-25 pep8 and flake8 fixes
    [DuckShootAlgoithm.py, LineFollowerCamera.py, MinimalMazeAlgorithm.py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]
2017-12-25 added pep8ify to list of scripts to run to correct formatting ran the updated autopep8 script
    [DuckShootAlgoithm.py, LineFollowerCamera.py, LineFollowerCameraAlg.py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]
2017-12-25 fixing some jenkins related issues
    [pylint.cfg]
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2017-12-26 updated pylint config file to ignore locally disabled warnings
    [pylint.cfg]
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2017-12-28 Fixed a few more warnings
    [pylint.cfg]
2017-12-28 fixed a few typos in comments
    [UltrasonicSensor.py]
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2018-01-05 Fixed bug in no contours and added processing time calculation.
    [SomewhereOverTheRainbowThread.py]
2018-01-06 fixed gpio switching following some testing on the pi
2018-01-08 Added schematics and updated scripts Also added GPIO values to the pins in the GPIOLayout.py file
    [rfc.kicad_pcb, rfc.sch]
2018-01-08 Capitolisation of a folder
    [rfc.kicad_pcb, rfc.sch]
2018-01-08 added servo veroboard required to connect to the pi when there isnt a robothat in the middle
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2018-01-12 Added 100mm Omni-directional wheels on short base.
2018-01-13 Updated schematic
    [rfc.sch]
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2018-01-18 Updated with correct ultrasonic mounts & holes.
2018-01-23 Updated StraightLineSpeedTestAlgorithm.py to use the dual motor configuration Added turn_forward and turn_reverse to the dual motor controller Added tests for new dual motor controller functions Upda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
2018-02-03 Added straight line speed test calculation spreadsheet in order to work out the effect of the combination of wheel diameter and motor rpm Speed
    Added visio diagram of how the motors and motor controller are wired up
    [SpeedTestCalculations.xlsx]
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2018-02-24 Nick's additions.
    [Nerf Holder.dxf, Pi Wars Chassis.dxf]
2018-02-24 Added power supply circuit, veraboard and pcb design
    [PowerSupplyAndSafeOff.dsn, PowerSupplyAndSafeOff.kicad_pcb, PowerSupplyAndSafeOff.sch]
2018-02-24 moved the main design into its own folder
    [rfc.kicad_pcb, rfc.sch]
2018-02-24 more moving of directories
    [rfc.kicad_pcb, rfc.sch]
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2018-02-24 Added interface board schematic and pcb
    [InterfaceBoard.dsn, InterfaceBoard.kicad_pcb, InterfaceBoard.sch]
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2018-02-25 Added tilt angle correction.
    [SomewhereOverTheRainbowThread.py]
2018-03-03 Layout of connections to GPIO pins.
    [GPIO Pins.xlsx]
2018-03-03 Linked to GPIOLayout.py & chose pin for DuckShoot.
    [GPIO Pins.xlsx]
2018-03-04 Duck shoot changes to electronics design
    [SpeedTestCalculations.xlsx, rfc.sch]
2018-03-04 Added ability to toggle both nerf drive motor and laser. Made the pins for the servos consistent
2018-03-04 Added RS order list
    [PartList.xlsx]
2018-03-04 Updated the veroboard circuits Updated the interface board design updated the RS parts list
    [InterfaceBoard.dsn, InterfaceBoard.kicad_pcb, InterfaceBoard.sch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]
2018-03-05 Switched to using BCM (GPIO) numbering rather than pin (BOARD) numbering as a number of libraries use BCM and this was conflicting with the current definitions. (This was the cause of the runtime fai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
    [rfc.sch]
2018-03-05 Fixed compile issue and missing logging
    [MotorController_test.py]
2018-03-05 Attempt to fix the missing c and z buttons on the nunchuk
    [DuckShootAlgoithm.py]
2018-03-06 Created a common wiimote controller interface and updated the duck shoot algorithm to use it. Modified the gpio handling to use a different gpiozero library as this allowed me to read the state back.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
2018-03-07 updated servod with latest code. Updated servo test to also test the nerf servo
2018-03-07 Updated servo interface to use correct gpiolaout define
    [GPIOLayout.py, ServoController.py]
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2018-03-07 updated gpio pin for the motor on off line
    [rfc.sch]
2018-03-07 Added a just drive python file and fixed minor issues associated with the duck shoot
    [DuckShootAlgoithm.py, JustDriving.py, WiimoteNunchukControllerThread.py]
2018-03-07 fixed sleeps to be infiniate rather than limited in the jusdt drive and duck shoot algos
    [DuckShootAlgoithm.py, JustDriving.py]
2018-03-08 Added some missing debug to the somewhere over the rainbow
    [SomewhereOverTheRainbowThread.py]
2018-03-08 Found a few more missing self. statements during debugging
    [SomewhereOverTheRainbowThread.py]
2018-03-09 Updated CameraThread as a precurser to the over the rainbow in order to de-couple the logic further
2018-03-09 Fixed random reverse at the start of anything using the wiimote interface
    [WiimoteNunchukControllerThread.py]
2018-03-09 Fixed issue with the pan and tilt getting mixed up.
    [GPIOLayout.py, ServoController.py, WiimoteNunchukControllerThread.py]
2018-03-10 Split out the Camera thread to a callback model and added a test. HAve reflected ethese changes into somewhere over the rainbow as well.
2018-03-10 Attempt to fix the seg fault at the completion of somewhere over the rainbow
    [SomewhereOverTheRainbowThread.py, UltrasonicSensor.py]
2018-03-11 Update to Slightly Deranged Golf design.
    [Slightly Deranged Golf - Layers.dxf]
2018-03-15 Needed for Servo calculations.
    [Nerf Gun.xlsx]
2018-03-25 Modified the camera callback code to only use the width and height in one place Modified the GPIO output code to allow active low interfaces
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2018-03-26 Fixed test issues with the servo controller
    [ServoController.py, ServoController_test.py]
2018-03-27 Fixed some pyline issues
    [ServoController.py]
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2018-04-09 Lots of pylint and pep8 fixes
    [pylint.cfg]
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2018-04-21 added web Links updated design files
    [rfc.sch]
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2019-03-02 added ui
    [bits bag.xlsx]
